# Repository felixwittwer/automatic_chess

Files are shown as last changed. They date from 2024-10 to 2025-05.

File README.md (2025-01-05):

# automatic_chess

## grbl firmware v1.1 for movement

[https://github.com/gnea/grbl](https://github.com/gnea/grbl)

Follow the original guide for installation and compilation: [https://github.com/gnea/grbl/wiki/Compiling-Grbl](https://github.com/gnea/grbl/wiki/Compiling-Grbl)

Instead of the original Repository the cusomt configuration in this repository should be used.

##
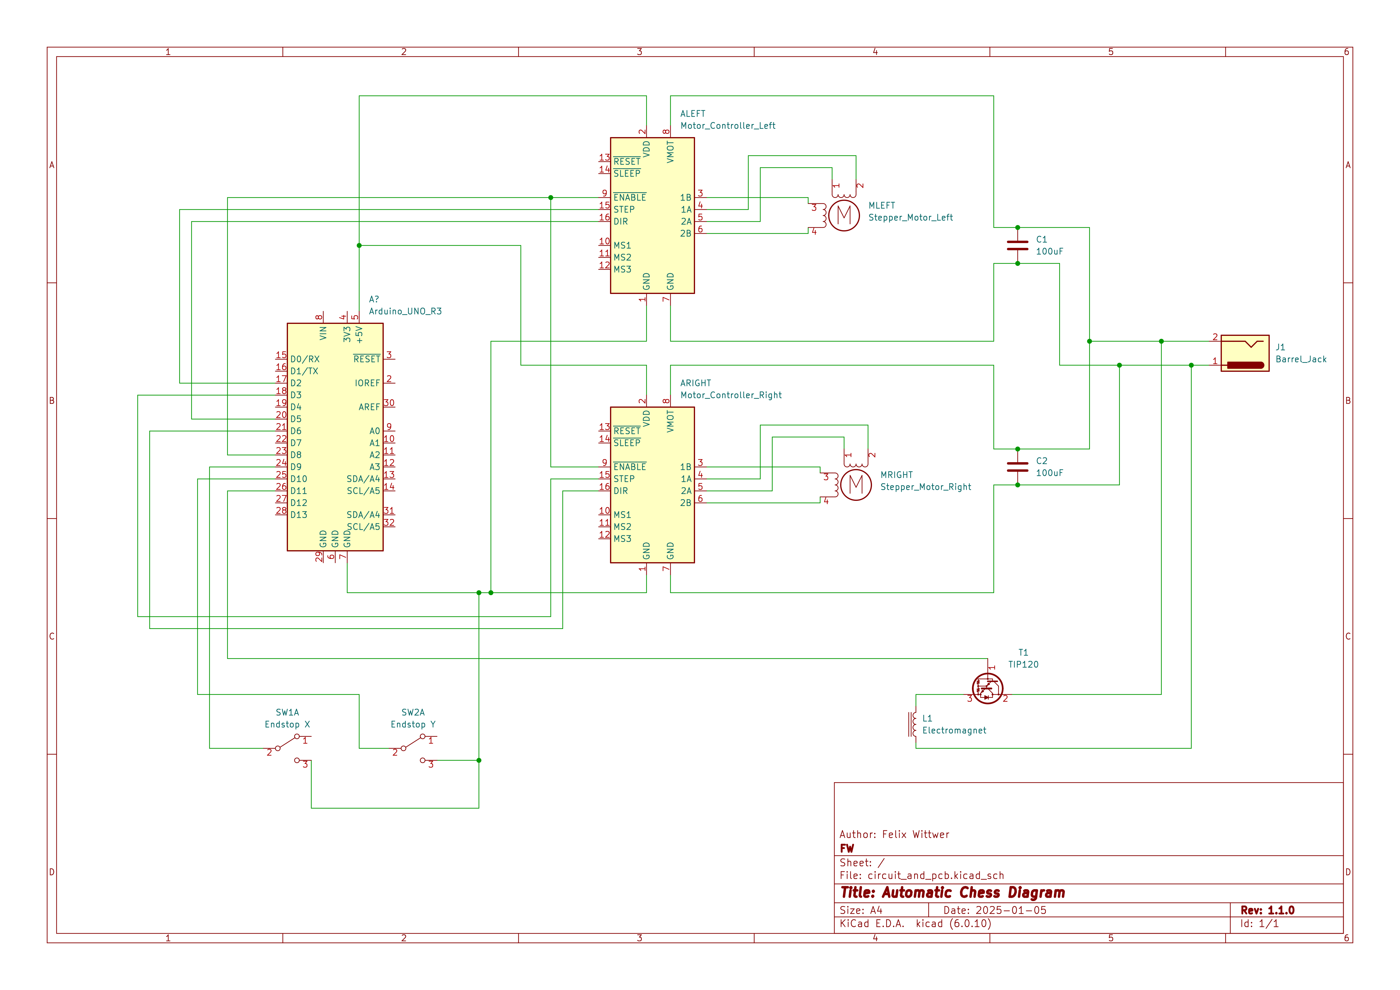
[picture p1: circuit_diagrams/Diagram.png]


[Diagram in PDF form](./circuit_diagrams/Diagram.pdf)

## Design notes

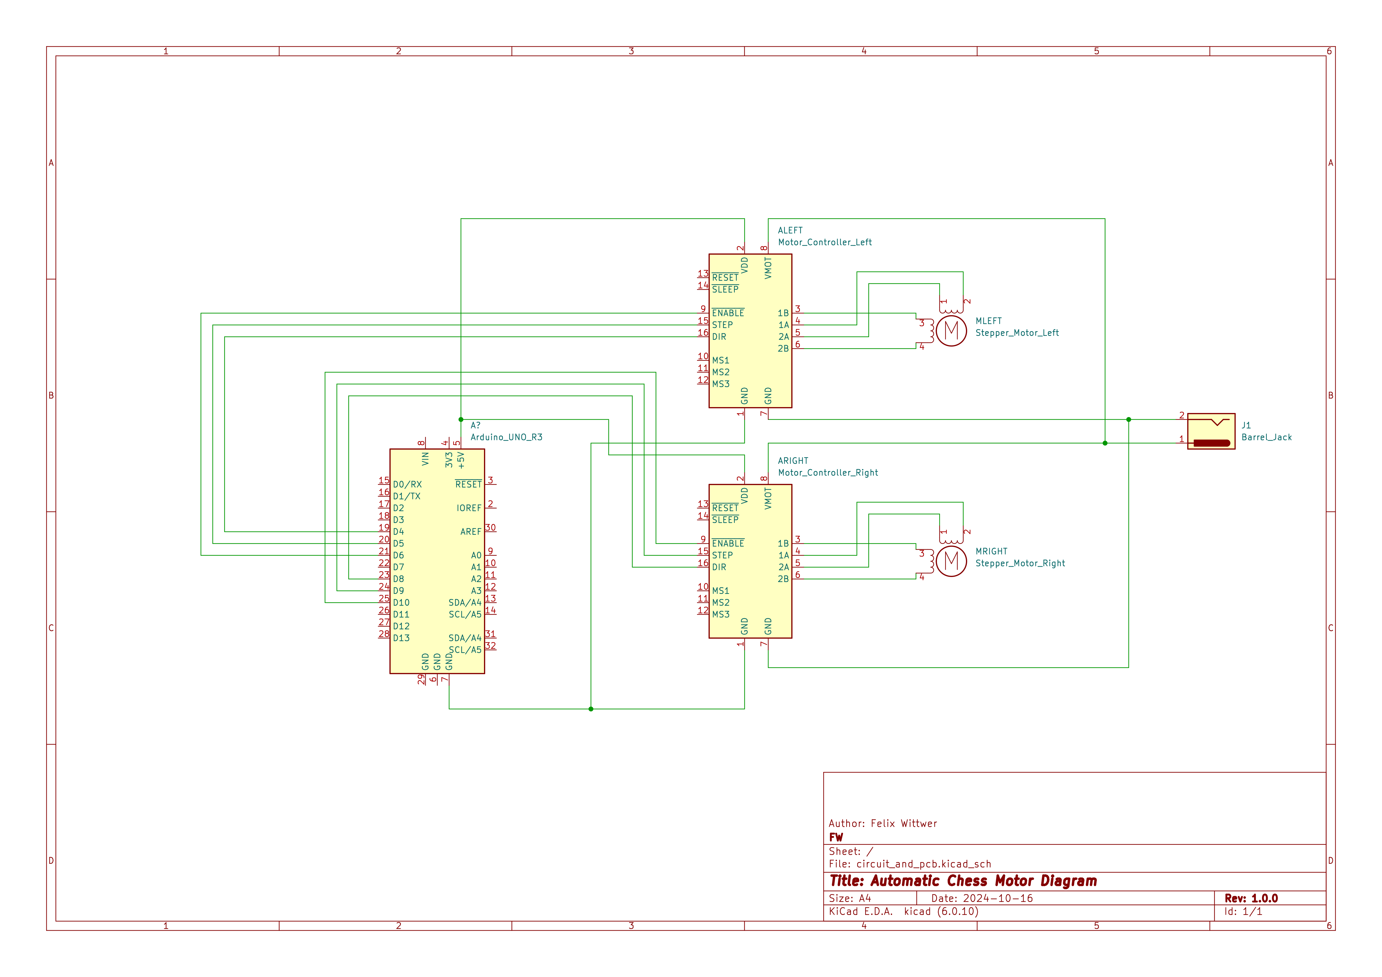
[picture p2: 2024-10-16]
circuit_diagrams/Motor_Diagram.png

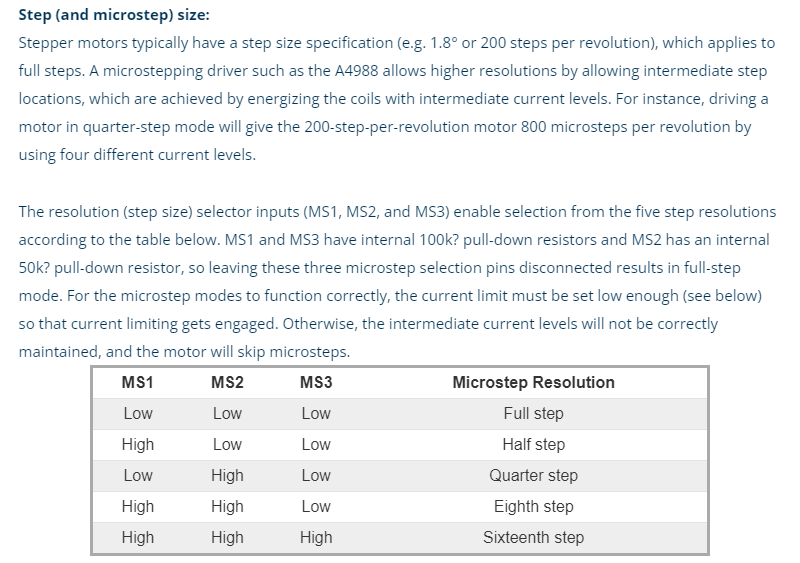
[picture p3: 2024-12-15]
datasheets/motor_driver_A4988/Stepsize.png

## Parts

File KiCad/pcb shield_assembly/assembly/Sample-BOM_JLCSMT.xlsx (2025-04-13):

Comment | Designator | Footprint | JLCPCB Part #（optional）
 | A2.3,A2.1,J17 | PinHeader_1x08_P2.54mm_Vertical
 | A2.4 | PinHeader_1x06_P2.54mm_Vertical
 | A2.2 | PinHeader_1x10_P2.54mm_Vertical
 | A4.2,A4.1,A3.2,A3.1,U4.2,U3.2,U2.2,U1.2 | PinSocket_1x08_P2.54mm_Vertical
 | U4.1,U3.1,U2.1,U1.1 | PinSocket_1x16_P2.54mm_Vertical
 | J14 | TerminalBlock_Phoenix_MKDS-1,5-2_1x02_P5.00mm_Horizontal
 | J4,J2,J6,J3,J8,J5,J1,J7 | PinHeader_2x04_P2.54mm_Vertical
 | J12 | PinHeader_1x02_P2.54mm_Vertical
 | J15,J16 | PinSocket_1x20_P2.54mm_Vertical
 | J19,J18 | PinHeader_1x06_P2.54mm_Vertical
100uF | C1,C2 | CP_Radial_D5.0mm_P2.50mm
 | J13 | PinHeader_1x02_P2.54mm_Vertical
 | J9 | PinHeader_1x02_P2.54mm_Vertical
 | RXD1 | TestPoint_Pad_D2.0mm
TIP120 | Q1 | TO-220-3_Vertical
 | 5V1,5V2 | TestPoint_Pad_D2.0mm
 | GND3,GND2,GND1 | TestPoint_Pad_D2.0mm
 | STEP2,STEP1 | TestPoint_Pad_D2.0mm
 | DIR2,DIR1 | TestPoint_Pad_D2.0mm
 | VMOT1 | TestPoint_Pad_D2.0mm
 | J10 | PinHeader_1x04_P2.54mm_Vertical
 | TXD1 | TestPoint_Pad_D2.0mm
 | J11 | PinHeader_1x04_P2.54mm_Vertical
 | A1 | PinSocket_2x20_P2.54mm_Vertical
100uF | C1 | CAP-SMD_L3.5-W2.8 | C16133

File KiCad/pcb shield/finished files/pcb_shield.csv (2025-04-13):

ID | Bezeichner | Gehäuse | Stückzahl | Bezeichnung | Anbieter und Referenz
1 | J14 | TerminalBlock_Phoenix_MKDS-1,5-2_1x02_P5.00mm_Horizontal | 1 | Barrel_Jack
2 | J4,J2,J6,J3,J8,J5,J1,J7 | PinHeader_2x04_P2.54mm_Vertical | 8
3 | J12 | PinHeader_1x02_P2.54mm_Vertical | 1 | Endstop X
4 | J15,J16 | PinSocket_1x20_P2.54mm_Vertical | 2 | Add Conn
5 | J19,J18 | PinHeader_1x06_P2.54mm_Vertical | 2 | Add Conn
6 | C1,C2 | CP_Radial_D5.0mm_P2.50mm | 2 | 100uF
7 | J13 | PinHeader_1x02_P2.54mm_Vertical | 1 | Endstop Y
8 | J9 | PinHeader_1x02_P2.54mm_Vertical | 1 | E_Magnet
9 | RXD1 | TestPoint_Pad_D2.0mm | 1 | RXD
10 | Q1 | TO-220-3_Vertical | 1 | TIP120
11 | 5V1,5V2 | TestPoint_Pad_D2.0mm | 2 | 5V
12 | GND3,GND2,GND1 | TestPoint_Pad_D2.0mm | 3 | GND
13 | STEP2,STEP1 | TestPoint_Pad_D2.0mm | 2 | STEP
14 | DIR2,DIR1 | TestPoint_Pad_D2.0mm | 2 | DIR
15 | VMOT1 | TestPoint_Pad_D2.0mm | 1 | VMOT
16 | J10 | PinHeader_1x04_P2.54mm_Vertical | 1 | Motor Conn L
17 | TXD1 | TestPoint_Pad_D2.0mm | 1 | TXD
18 | A4 | Pololu_Breakout-16_15.2x20.3mm | 1 | Motor Controller Right
19 | A3 | Pololu_Breakout-16_15.2x20.3mm | 1 | Motor Controller Left
20 | J11 | PinHeader_1x04_P2.54mm_Vertical | 1 | Motor Conn R
21 | J17 | PinHeader_1x08_P2.54mm_Vertical | 1 | Add Conn
22 | U1,U4,U3,U2 | MODULE_BOB-09056 | 4 | BOB-09056
23 | A1 | PinSocket_2x20_P2.54mm_Vertical | 1 | Raspberry Pi Zero
24 | A2 | Arduino_UNO_R3 | 1 | Arduino_UNO_R3

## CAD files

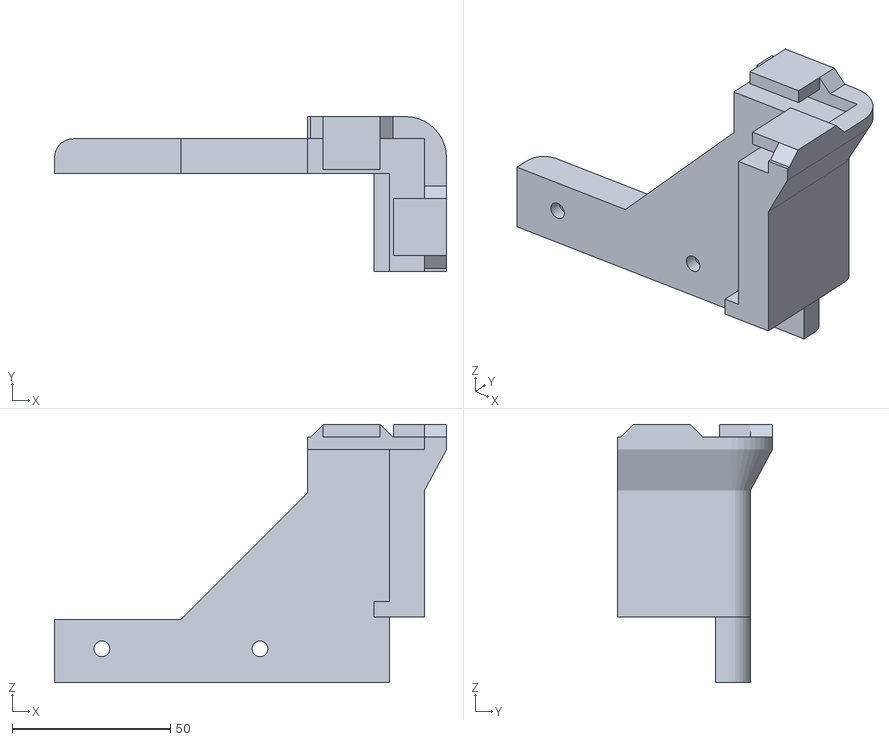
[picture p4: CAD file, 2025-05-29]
3d_files/Plexiglasmount/A_Plexiglasmount.stl
124.0 x 49.0 x 81.7

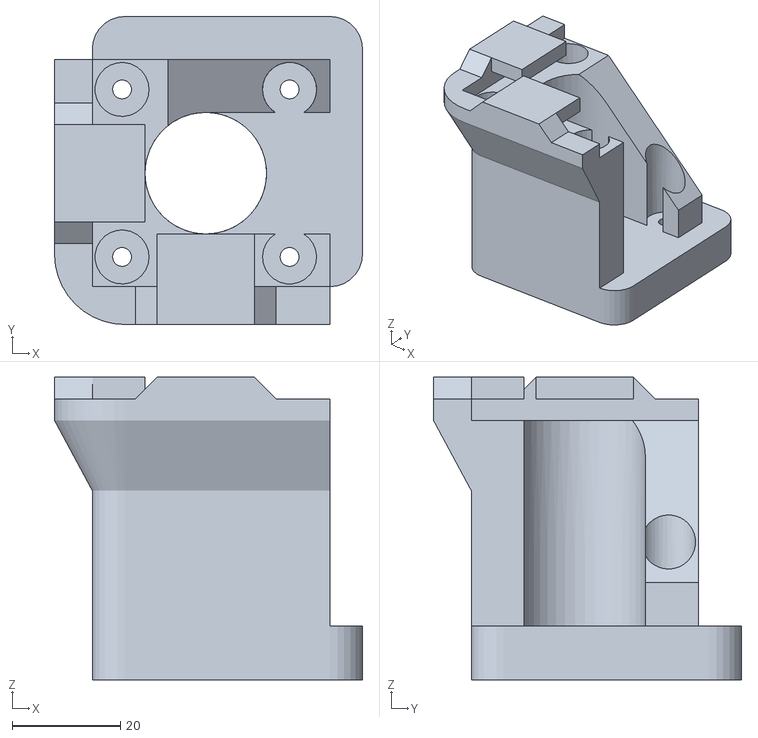
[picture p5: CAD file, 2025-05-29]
3d_files/Plexiglasmount/Motor_B_Plexiglasmount.stl
57.0 x 57.0 x 56.0

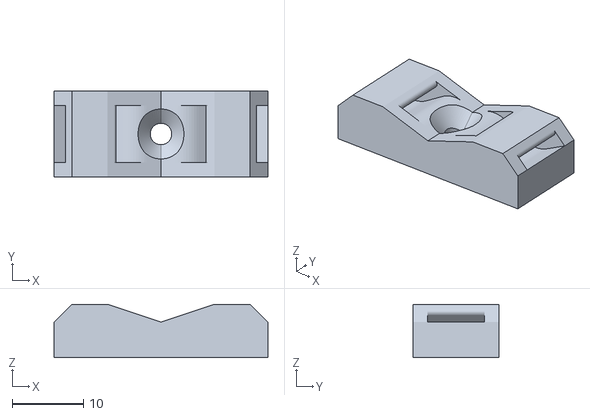
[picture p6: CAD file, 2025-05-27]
3d_files/PCB holder and cable organizers/Cable_clips_for_zipties.stl
30.0 x 12.0 x 7.50

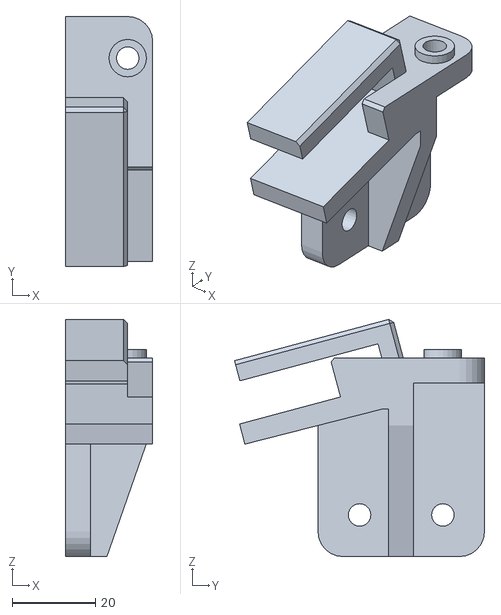
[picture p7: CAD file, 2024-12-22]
3d_files/Pulley_Support_A_new.stl
21.0 x 60.1 x 57.0

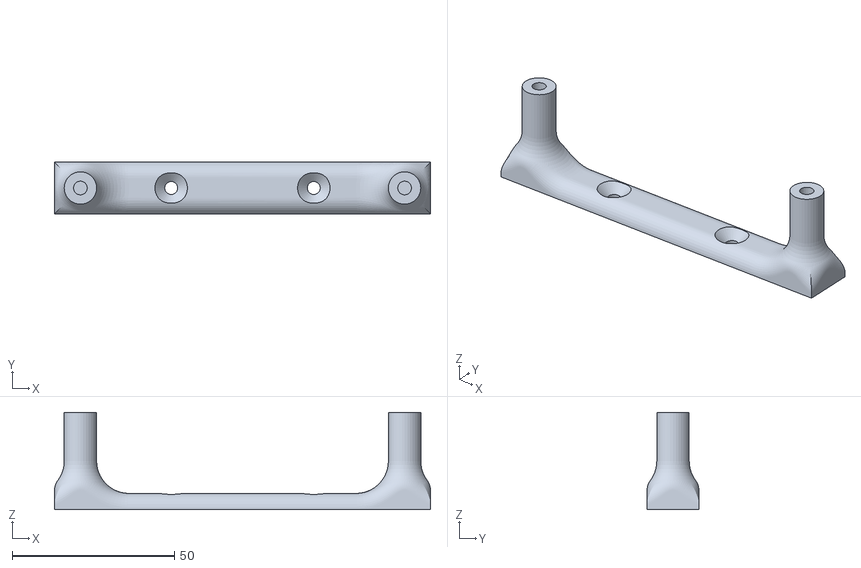
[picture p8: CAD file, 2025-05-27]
3d_files/PCB holder and cable organizers/PCB_holder.stl
116.0 x 16.0 x 30.0

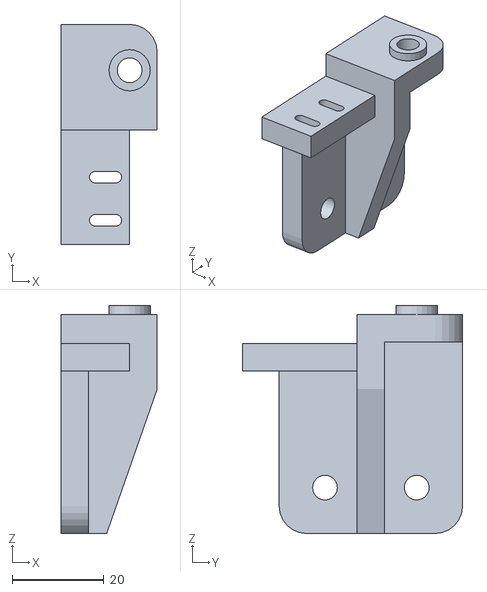
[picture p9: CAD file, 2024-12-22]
3d_files/Pulley_Support_A.stl
21.0 x 48.0 x 49.7

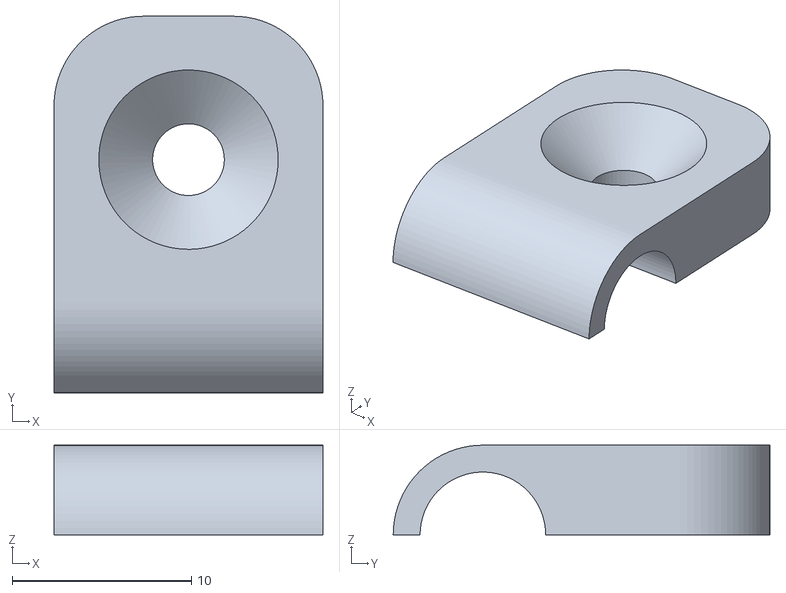
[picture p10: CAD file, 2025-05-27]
3d_files/PCB holder and cable organizers/small cable clip.stl
15.0 x 21.0 x 5.00

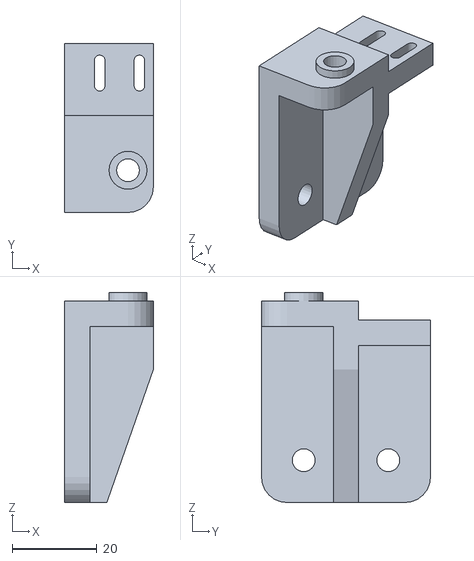
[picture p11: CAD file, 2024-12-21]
3d_files/Pulley_Support_B.stl
21.0 x 40.0 x 49.7

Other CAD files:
3d_files/Plexiglasmount/Motor_A_Plexiglasmount.stl
3d_files/Plexiglasmount/B_Plexiglasmount.stl
3d_files/Pulley_Support_B_new.stl

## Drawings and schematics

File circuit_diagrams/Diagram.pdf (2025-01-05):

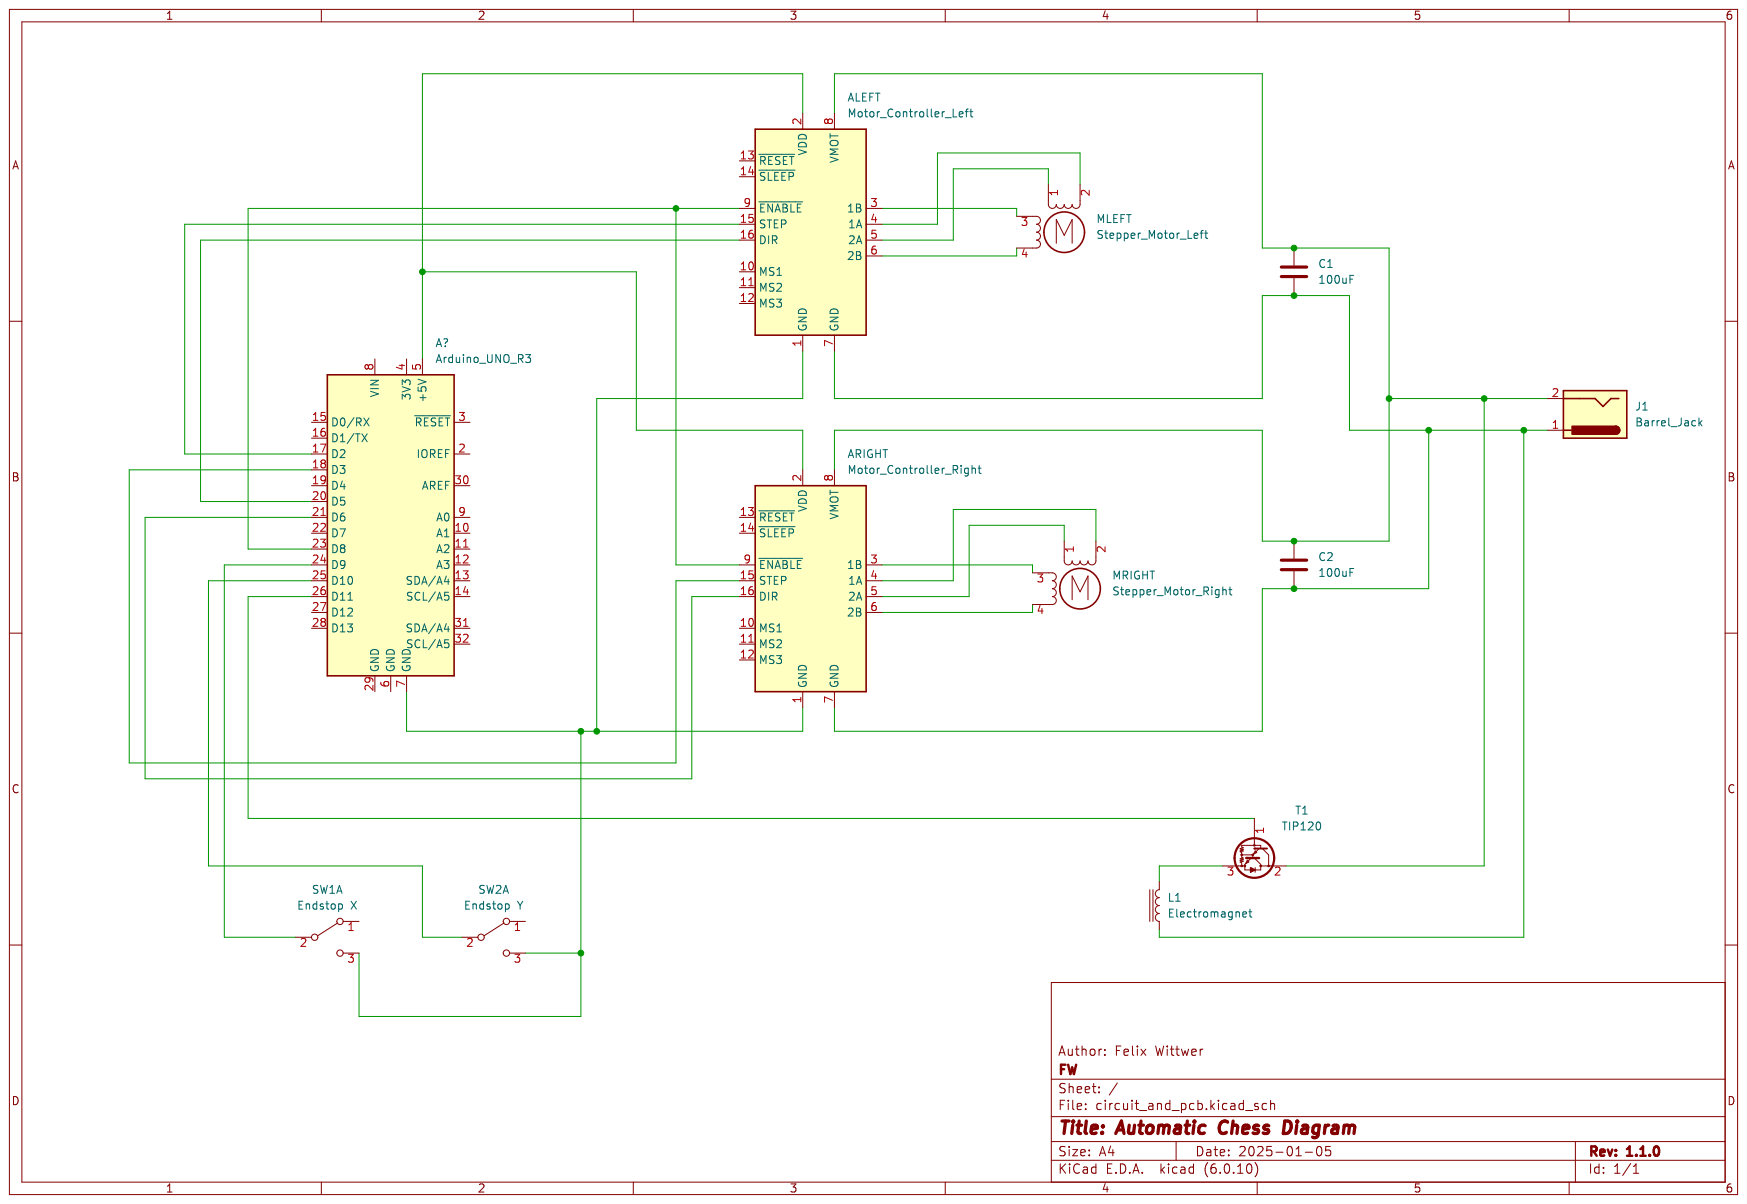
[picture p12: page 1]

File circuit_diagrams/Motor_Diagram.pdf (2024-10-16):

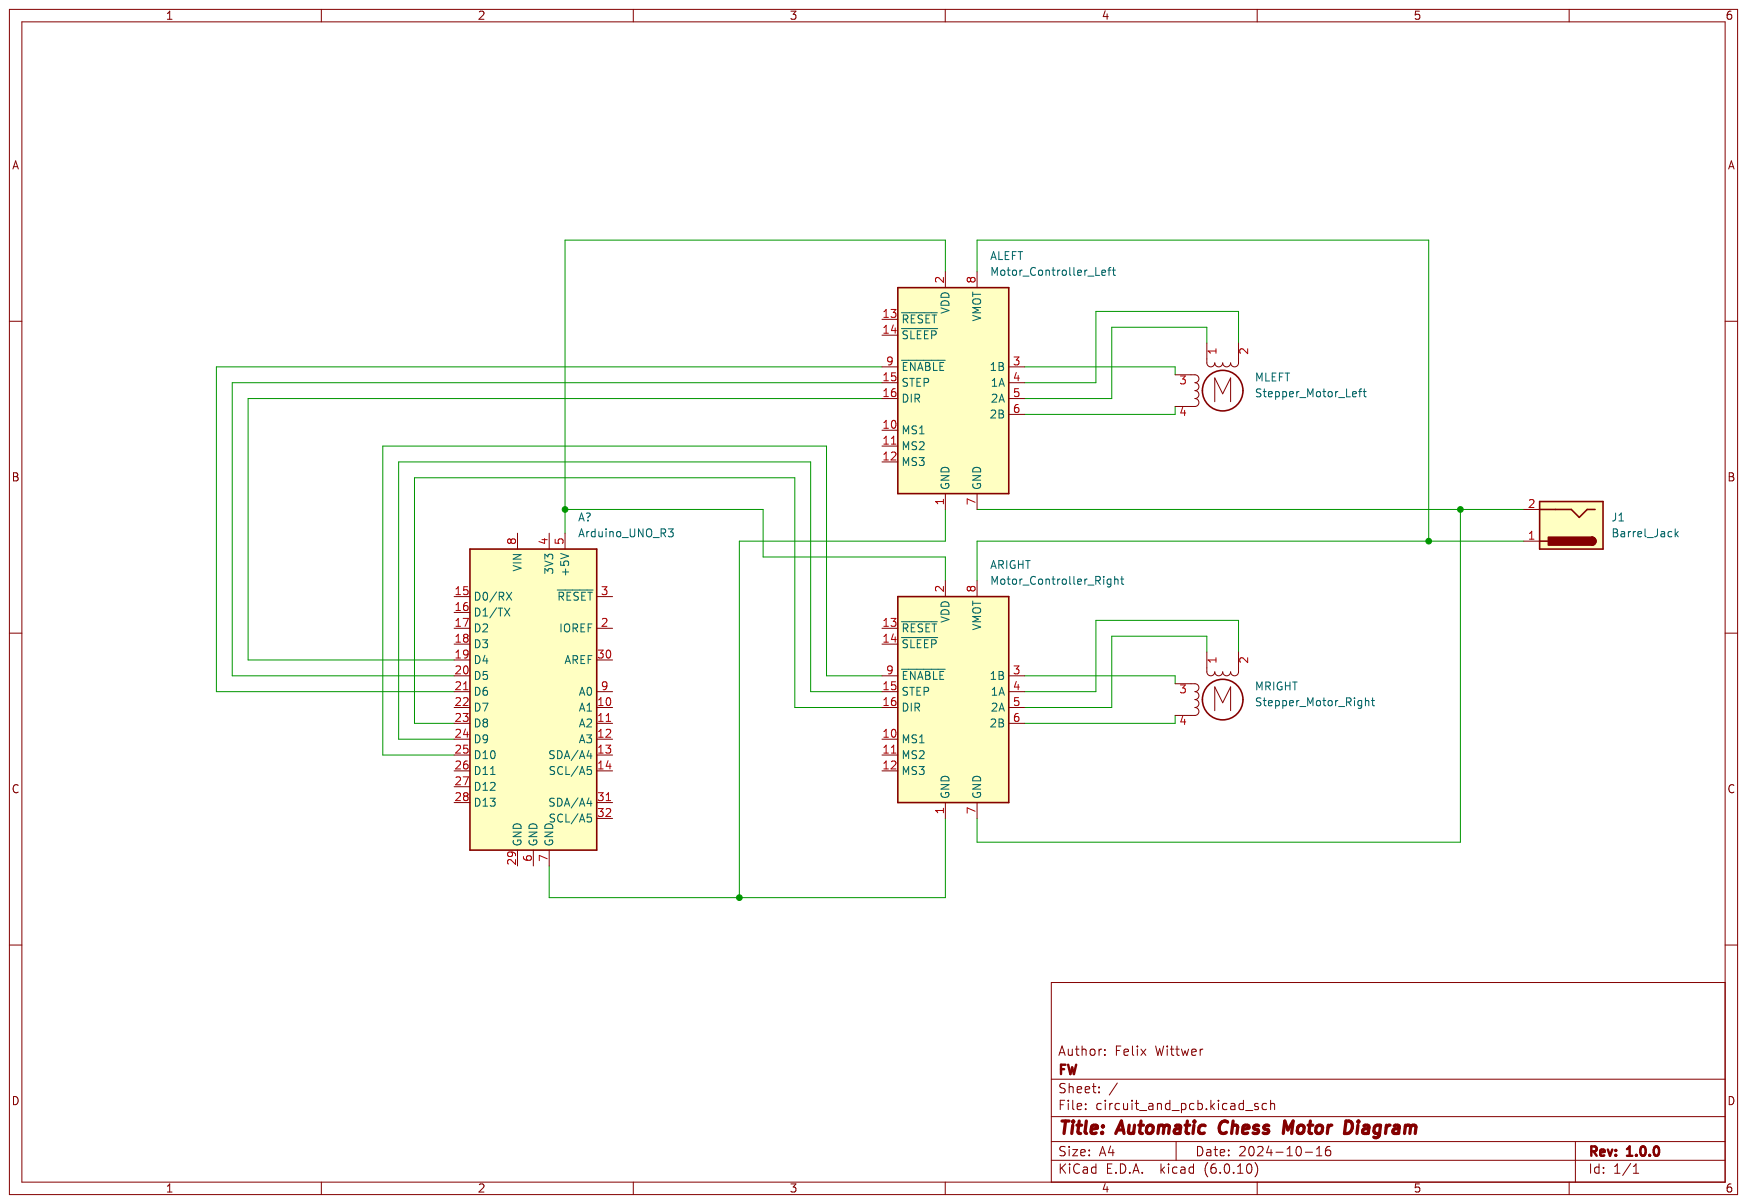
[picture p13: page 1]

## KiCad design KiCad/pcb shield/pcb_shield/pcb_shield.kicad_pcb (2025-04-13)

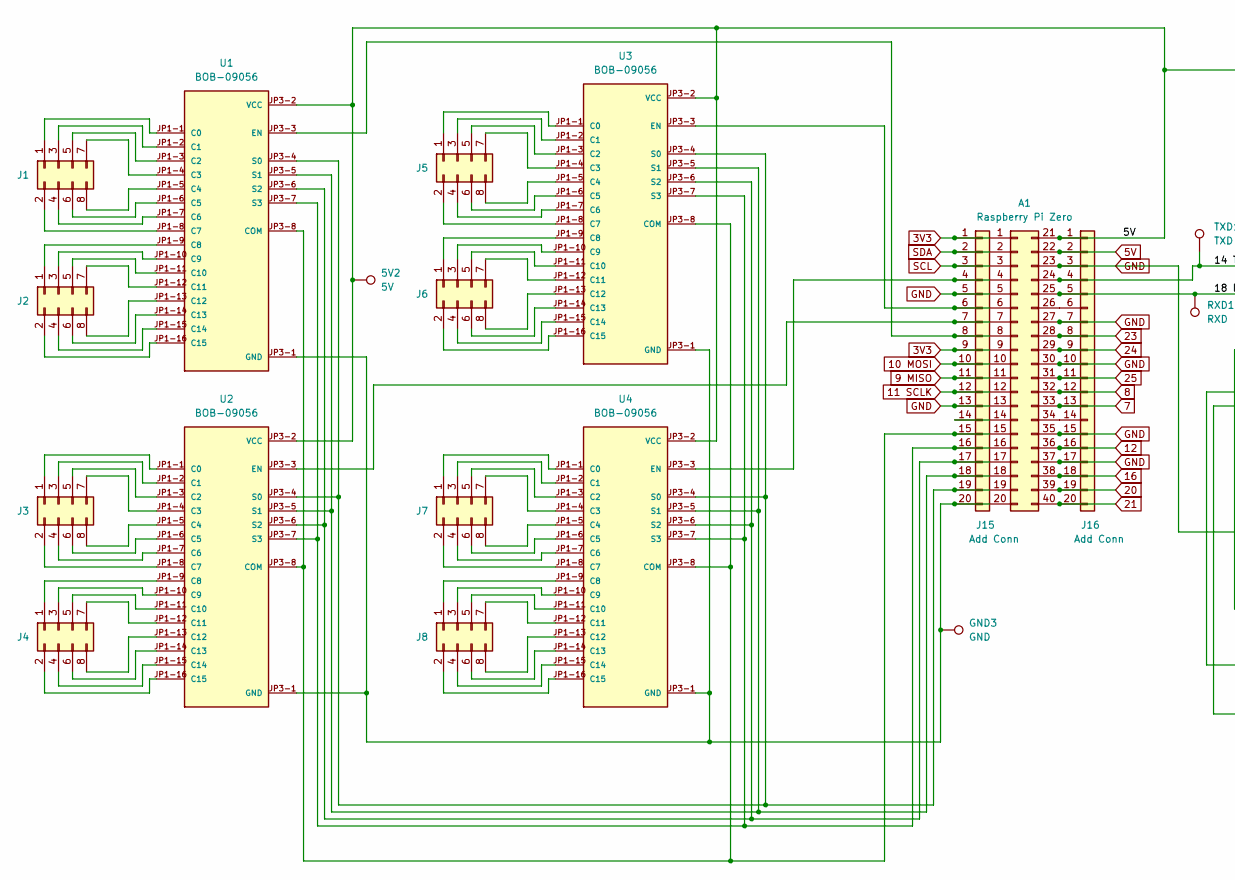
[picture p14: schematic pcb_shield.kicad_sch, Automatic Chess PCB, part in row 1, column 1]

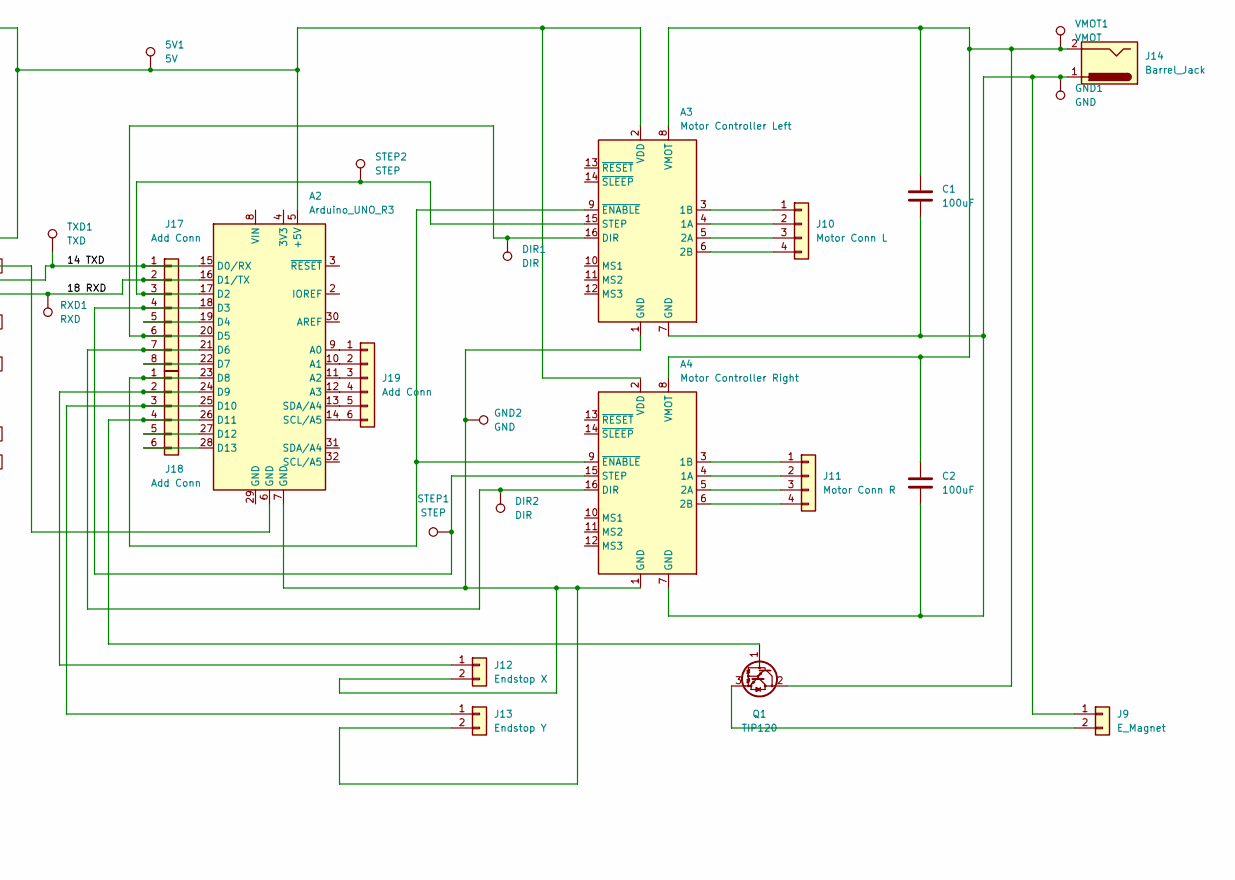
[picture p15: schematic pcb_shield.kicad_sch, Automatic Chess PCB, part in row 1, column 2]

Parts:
5V1, 5V2: 5V; TestPoint_Pad_D2.0mm
A1: Raspberry Pi Zero; PinSocket_2x20_P2.54mm_Vertical
A2: Arduino_UNO_R3
A3: Motor Controller Left; Pololu_Breakout-16_15.2x20.3mm
A4: Motor Controller Right; Pololu_Breakout-16_15.2x20.3mm
C1, C2: 100uF; CP_Radial_D5.0mm_P2.50mm
DIR1, DIR2: DIR; TestPoint_Pad_D2.0mm
GND1, GND2, GND3: GND; TestPoint_Pad_D2.0mm
J1, J2, J3, J4, J5, J6, J7, J8: PinHeader_2x04_P2.54mm_Vertical
J9: E_Magnet; PinHeader_1x02_P2.54mm_Vertical
J10: Motor Conn L; PinHeader_1x04_P2.54mm_Vertical
J11: Motor Conn R; PinHeader_1x04_P2.54mm_Vertical
J12: Endstop X; PinHeader_1x02_P2.54mm_Vertical
J13: Endstop Y; PinHeader_1x02_P2.54mm_Vertical
J14: Barrel_Jack; TerminalBlock_Phoenix_MKDS-1,5-2_1x02_P5.00mm_Horizontal
J15, J16: Add Conn; PinSocket_1x20_P2.54mm_Vertical
J17: Add Conn; PinHeader_1x08_P2.54mm_Vertical
J18, J19: Add Conn; PinHeader_1x06_P2.54mm_Vertical
Q1: TIP120; TO-220-3_Vertical
RXD1: RXD; TestPoint_Pad_D2.0mm
STEP1, STEP2: STEP; TestPoint_Pad_D2.0mm
TXD1: TXD; TestPoint_Pad_D2.0mm
U1, U2, U3, U4: BOB-09056; MODULE_BOB-09056; PARTREV v11
VMOT1: VMOT; TestPoint_Pad_D2.0mm

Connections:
3V3: A1.1, A1.9, J15.1, J15.9
5V: 5V1.1, 5V2.1, A1.21, A1.22, A2.5 (+5V), A3.2 (VDD), A4.2 (VDD), J16.1, J16.2, U1.JP3-2 (VCC), U2.JP3-2 (VCC), U3.JP3-2 (VCC), U4.JP3-2 (VCC)
7: A1.33, J16.13
8: A1.32, J16.12
9 MISO: A1.11, J15.11
10 MOSI: A1.10, J15.10
11 SCLK: A1.12, J15.12
12: A1.36, J16.16
16: A1.38, J16.18
20: A1.39, J16.19
21: A1.40, J16.20
23: A1.28, J16.8
24: A1.29, J16.9
25: A1.31, J16.11
/14 TXD: A1.24, A2.15 (D0/RX), J16.4, J17.1, TXD1.1
/18 RXD: A1.25, A2.16 (D1/TX), J16.5, J17.2, RXD1.1
GND: A1.5, A1.13, A1.23, A1.27, A1.30, A1.35, A1.37, A2.6 (GND), J15.5, J15.13, J16.3, J16.7, J16.10, J16.15, J16.17
unnamed: A1.4, J15.4, U4.JP3-3 (EN)
unnamed: A1.6, J15.6, U3.JP3-3 (EN)
unnamed: A1.7, J15.7, U2.JP3-3 (EN)
unnamed: A1.8, J15.8, U1.JP3-3 (EN)
unnamed: A1.14, J15.14
unnamed: A1.15, J15.15, U1.JP3-8 (COM), U2.JP3-8 (COM), U3.JP3-8 (COM), U4.JP3-8 (COM)
unnamed: A1.16, J15.16, U1.JP3-7 (S3), U2.JP3-7 (S3), U3.JP3-7 (S3), U4.JP3-7 (S3)
unnamed: A1.17, J15.17, U1.JP3-6 (S2), U2.JP3-6 (S2), U3.JP3-6 (S2), U4.JP3-6 (S2)
unnamed: A1.18, J15.18, U1.JP3-5 (S1), U2.JP3-5 (S1), U3.JP3-5 (S1), U4.JP3-5 (S1)
unnamed: A1.19, J15.19, U1.JP3-4 (S0), U2.JP3-4 (S0), U3.JP3-4 (S0), U4.JP3-4 (S0)
unnamed: A1.20, GND3.1, J15.20, U1.JP3-1 (GND), U2.JP3-1 (GND), U3.JP3-1 (GND), U4.JP3-1 (GND)
unnamed: A1.26, J16.6
unnamed: A1.34, J16.14
unnamed: A2.7 (GND), A3.1 (GND), A4.1 (GND), GND2.1, J12.2, J13.2
unnamed: A2.9 (A0), J19.1
unnamed: A2.10 (A1), J19.2
unnamed: A2.11 (A2), J19.3
unnamed: A2.12 (A3), J19.4
unnamed: A2.13 (SDA/A4), J19.5
unnamed: A2.14 (SCL/A5), J19.6
unnamed: A2.17 (D2), A3.15 (STEP), J17.3, STEP2.1
unnamed: A2.18 (D3), A4.15 (STEP), J17.4, STEP1.1
unnamed: A2.19 (D4), J17.5
unnamed: A2.20 (D5), A3.16 (DIR), DIR1.1, J17.6
unnamed: A2.21 (D6), A4.16 (DIR), DIR2.1, J17.7
unnamed: A2.22 (D7), J17.8
unnamed: A2.23 (D8), A3.9 (~ENABLE), A4.9 (~ENABLE), J18.1
unnamed: A2.24 (D9), J12.1, J18.2
unnamed: A2.25 (D10), J13.1, J18.3
unnamed: A2.26 (D11), J18.4, Q1.1 (B)
unnamed: A2.27 (D12), J18.5
unnamed: A2.28 (D13), J18.6
unnamed: A3.3 (1B), J10.1
unnamed: A3.4 (1A), J10.2
unnamed: A3.5 (2A), J10.3
unnamed: A3.6 (2B), J10.4
unnamed: A3.7 (GND), A4.7 (GND), C1.2, C2.2, GND1.1, J9.1, J14.1
unnamed: A3.8 (VMOT), A4.8 (VMOT), C1.1, C2.1, J14.2, Q1.2 (C), VMOT1.1
unnamed: A4.3 (1B), J11.1
unnamed: A4.4 (1A), J11.2
unnamed: A4.5 (2A), J11.3
unnamed: A4.6 (2B), J11.4
unnamed: J1.1, U1.JP1-1 (C0)
unnamed: J1.2, U1.JP1-8 (C7)
unnamed: J1.3, U1.JP1-2 (C1)
unnamed: J1.4, U1.JP1-7 (C6)
unnamed: J1.5, U1.JP1-3 (C2)
unnamed: J1.6, U1.JP1-6 (C5)
unnamed: J1.7, U1.JP1-4 (C3)
unnamed: J1.8, U1.JP1-5 (C4)
unnamed: J2.1, U1.JP1-9 (C8)
unnamed: J2.2, U1.JP1-16 (C15)
unnamed: J2.3, U1.JP1-10 (C9)
unnamed: J2.4, U1.JP1-15 (C14)
unnamed: J2.5, U1.JP1-11 (C10)
unnamed: J2.6, U1.JP1-14 (C13)
unnamed: J2.7, U1.JP1-12 (C11)
unnamed: J2.8, U1.JP1-13 (C12)
unnamed: J3.1, U2.JP1-1 (C0)
unnamed: J3.2, U2.JP1-8 (C7)
unnamed: J3.3, U2.JP1-2 (C1)
unnamed: J3.4, U2.JP1-7 (C6)
unnamed: J3.5, U2.JP1-3 (C2)
unnamed: J3.6, U2.JP1-6 (C5)
unnamed: J3.7, U2.JP1-4 (C3)
unnamed: J3.8, U2.JP1-5 (C4)
unnamed: J4.1, U2.JP1-9 (C8)
unnamed: J4.2, U2.JP1-16 (C15)
unnamed: J4.3, U2.JP1-10 (C9)
unnamed: J4.4, U2.JP1-15 (C14)
unnamed: J4.5, U2.JP1-11 (C10)
unnamed: J4.6, U2.JP1-14 (C13)
unnamed: J4.7, U2.JP1-12 (C11)
unnamed: J4.8, U2.JP1-13 (C12)
unnamed: J5.1, U3.JP1-1 (C0)
unnamed: J5.2, U3.JP1-8 (C7)
unnamed: J5.3, U3.JP1-2 (C1)
unnamed: J5.4, U3.JP1-7 (C6)
unnamed: J5.5, U3.JP1-3 (C2)
unnamed: J5.6, U3.JP1-6 (C5)
unnamed: J5.7, U3.JP1-4 (C3)
unnamed: J5.8, U3.JP1-5 (C4)
unnamed: J6.1, U3.JP1-9 (C8)
unnamed: J6.2, U3.JP1-16 (C15)
unnamed: J6.3, U3.JP1-10 (C9)
unnamed: J6.4, U3.JP1-15 (C14)
unnamed: J6.5, U3.JP1-11 (C10)
unnamed: J6.6, U3.JP1-14 (C13)
unnamed: J6.7, U3.JP1-12 (C11)
unnamed: J6.8, U3.JP1-13 (C12)
unnamed: J7.1, U4.JP1-1 (C0)
unnamed: J7.2, U4.JP1-8 (C7)
unnamed: J7.3, U4.JP1-2 (C1)
unnamed: J7.4, U4.JP1-7 (C6)
unnamed: J7.5, U4.JP1-3 (C2)
unnamed: J7.6, U4.JP1-6 (C5)
unnamed: J7.7, U4.JP1-4 (C3)
unnamed: J7.8, U4.JP1-5 (C4)
unnamed: J8.1, U4.JP1-9 (C8)
unnamed: J8.2, U4.JP1-16 (C15)
unnamed: J8.3, U4.JP1-10 (C9)
unnamed: J8.4, U4.JP1-15 (C14)
unnamed: J8.5, U4.JP1-11 (C10)
unnamed: J8.6, U4.JP1-14 (C13)
unnamed: J8.7, U4.JP1-12 (C11)
unnamed: J8.8, U4.JP1-13 (C12)
unnamed: J9.2, Q1.3 (E)
SCL: A1.3, J15.3
SDA: A1.2, J15.2

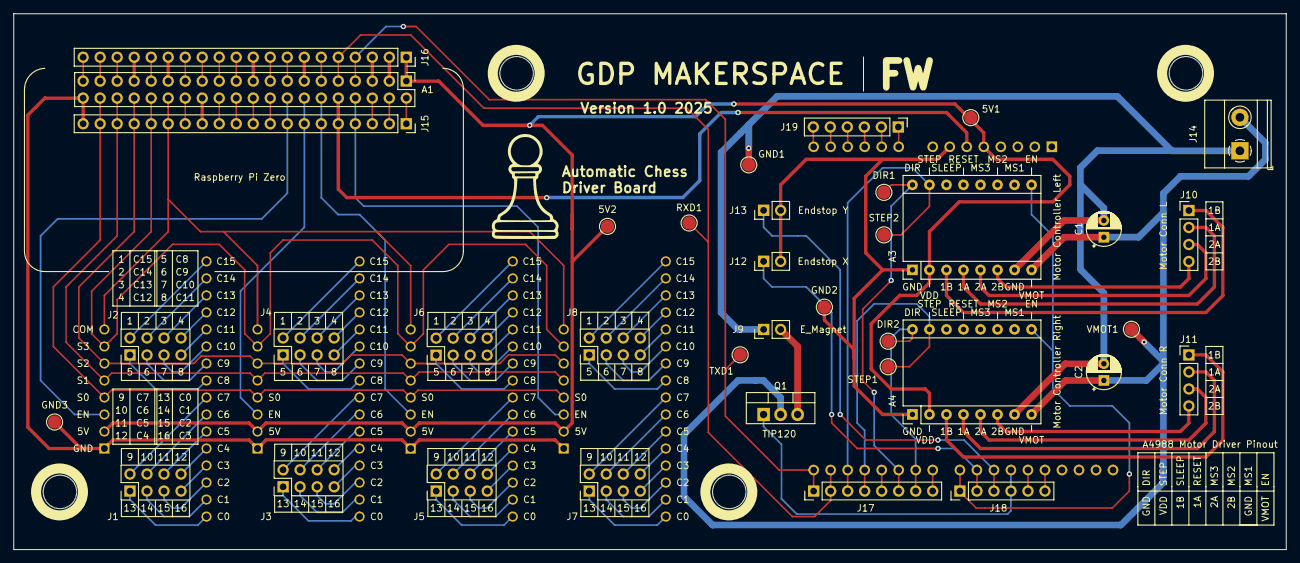
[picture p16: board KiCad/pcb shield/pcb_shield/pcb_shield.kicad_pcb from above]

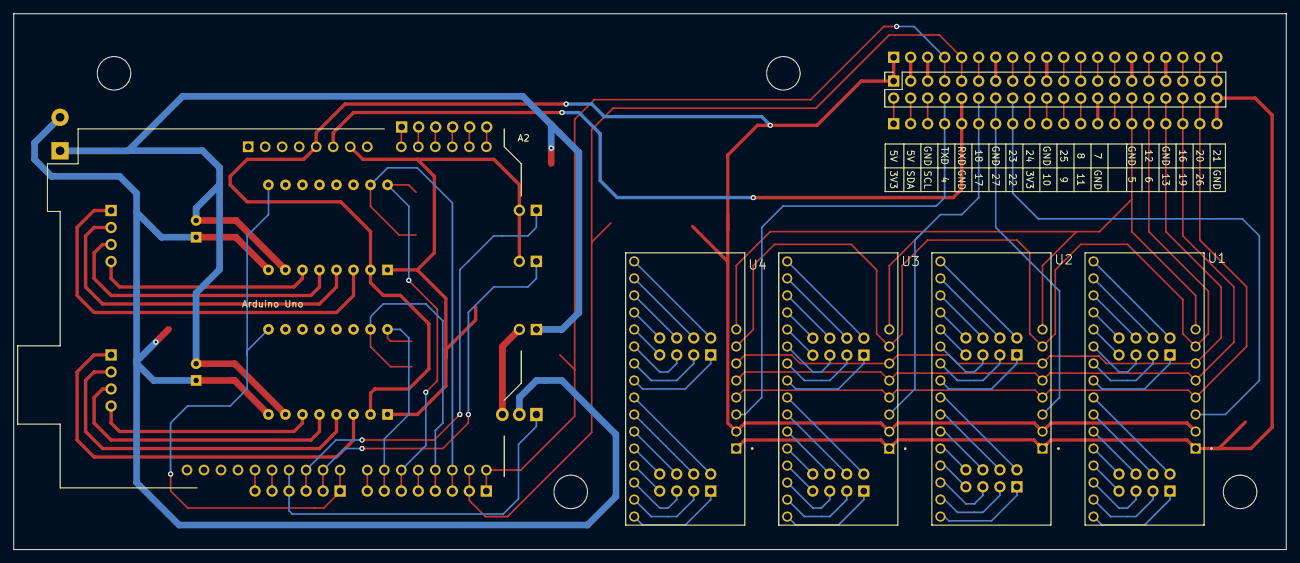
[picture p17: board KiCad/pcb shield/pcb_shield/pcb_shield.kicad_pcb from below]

Board: 2 copper layers, 190.0 x 80.0 mm, 42 parts (6 on the bottom side), 126 nets.

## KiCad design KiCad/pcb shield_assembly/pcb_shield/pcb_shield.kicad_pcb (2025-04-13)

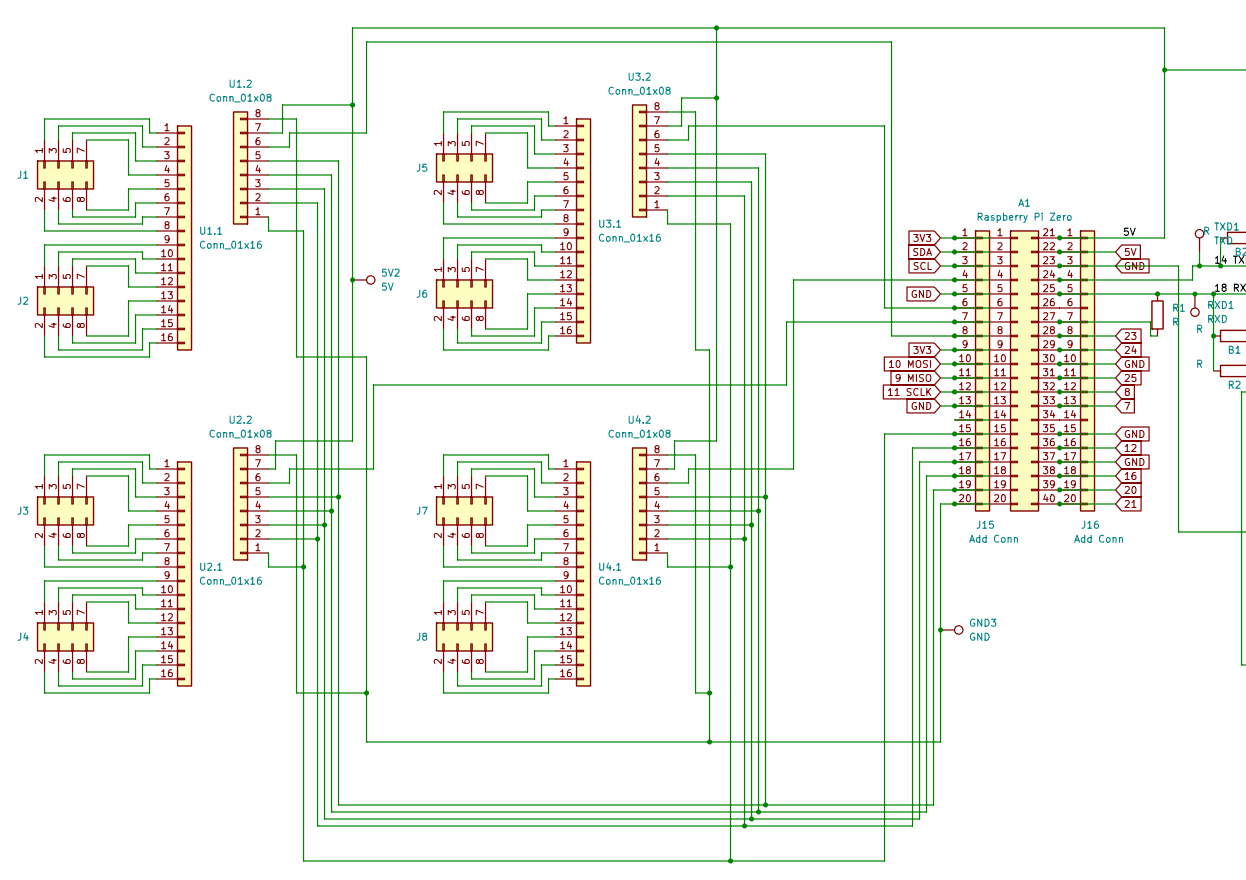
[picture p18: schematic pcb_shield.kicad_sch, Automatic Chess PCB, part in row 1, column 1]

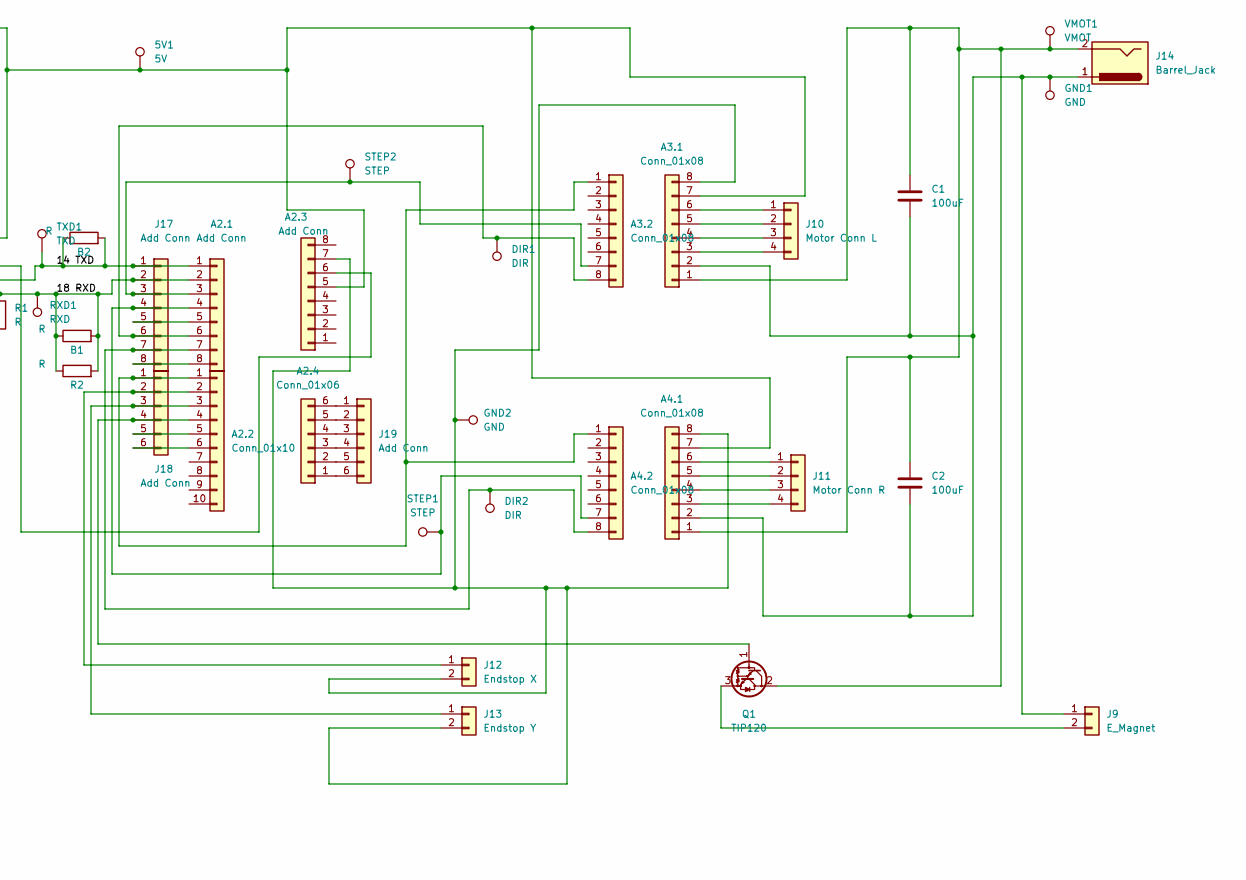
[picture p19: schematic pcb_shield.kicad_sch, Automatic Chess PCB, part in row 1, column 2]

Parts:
5V1, 5V2: 5V; TestPoint_Pad_D2.0mm
A1: Raspberry Pi Zero; PinSocket_2x20_P2.54mm_Vertical
A2.1, A2.3: Add Conn; PinHeader_1x08_P2.54mm_Vertical
A2.2: Conn_01x10; PinHeader_1x10_P2.54mm_Vertical
A2.4: Conn_01x06; PinHeader_1x06_P2.54mm_Vertical
A3.1, A3.2, A4.1, A4.2: Conn_01x08; PinSocket_1x08_P2.54mm_Vertical
B1, B2: R; R_1206_3216Metric_Pad1.30x1.75mm_HandSolder
C1, C2: 100uF; CP_Radial_D5.0mm_P2.50mm
DIR1, DIR2: DIR; TestPoint_Pad_D2.0mm
GND1, GND2, GND3: GND; TestPoint_Pad_D2.0mm
J1, J2, J3, J4, J5, J6, J7, J8: PinHeader_2x04_P2.54mm_Vertical
J9: E_Magnet; PinHeader_1x02_P2.54mm_Vertical
J10: Motor Conn L; PinHeader_1x04_P2.54mm_Vertical
J11: Motor Conn R; PinHeader_1x04_P2.54mm_Vertical
J12: Endstop X; PinHeader_1x02_P2.54mm_Vertical
J13: Endstop Y; PinHeader_1x02_P2.54mm_Vertical
J14: Barrel_Jack; TerminalBlock_Phoenix_MKDS-1,5-2_1x02_P5.00mm_Horizontal
J15, J16: Add Conn; PinSocket_1x20_P2.54mm_Vertical
J17: Add Conn; PinHeader_1x08_P2.54mm_Vertical
J18, J19: Add Conn; PinHeader_1x06_P2.54mm_Vertical
Q1: TIP120; TO-220-3_Vertical
R1, R2: R; R_Axial_DIN0309_L9.0mm_D3.2mm_P12.70mm_Horizontal
RXD1: RXD; TestPoint_Pad_D2.0mm
STEP1, STEP2: STEP; TestPoint_Pad_D2.0mm
TXD1: TXD; TestPoint_Pad_D2.0mm
U1.1, U2.1, U3.1, U4.1: Conn_01x16; PinSocket_1x16_P2.54mm_Vertical
U1.2, U2.2, U3.2, U4.2: Conn_01x08; PinSocket_1x08_P2.54mm_Vertical
VMOT1: VMOT; TestPoint_Pad_D2.0mm

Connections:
3V3: A1.1, A1.9, J15.1, J15.9
5V: 5V1.1, 5V2.1, A1.21, A1.22, A2.3.5, A3.1.7, A4.1.7, J16.1, J16.2, U1.2.7, U2.2.7, U3.2.7, U4.2.7
7: A1.33, J16.13
8: A1.32, J16.12
9 MISO: A1.11, J15.11
10 MOSI: A1.10, J15.10
11 SCLK: A1.12, J15.12
12: A1.36, J16.16
16: A1.38, J16.18
20: A1.39, J16.19
21: A1.40, J16.20
23: A1.28, J16.8
24: A1.29, J16.9
25: A1.31, J16.11
/14 TXD: A1.24, A2.1.1, B2.1, B2.2, J16.4, J17.1, TXD1.1
/18 RXD: A1.25, A2.1.2, B1.1, B1.2, J16.5, J17.2, R1.1, R2.1, R2.2, RXD1.1
GND: A1.5, A1.13, A1.23, A1.30, A1.35, A1.37, A2.3.6, J15.5, J15.13, J16.3, J16.10, J16.15, J16.17
unnamed: A1.4, J15.4, U4.2.6
unnamed: A1.6, J15.6, U3.2.6
unnamed: A1.7, J15.7, U2.2.6
unnamed: A1.14, J15.14
unnamed: A1.15, J15.15, U1.2.1, U2.2.1, U3.2.1, U4.2.1
unnamed: A1.16, J15.16, U1.2.2, U2.2.2, U3.2.2, U4.2.2
unnamed: A1.17, J15.17, U1.2.3, U2.2.3, U3.2.3, U4.2.3
unnamed: A1.18, J15.18, U1.2.4, U2.2.4, U3.2.4, U4.2.4
unnamed: A1.19, J15.19, U1.2.5, U2.2.5, U3.2.5, U4.2.5
unnamed: A1.20, GND3.1, J15.20, U1.2.8, U2.2.8, U3.2.8, U4.2.8
unnamed: A1.26, J16.6
unnamed: A1.27, J16.7, R1.2
unnamed: A1.34, J16.14
unnamed: A2.3.7, A3.1.8, A4.1.8, GND2.1, J12.2, J13.2
unnamed: A3.1.1, A4.1.1, C1.1, C2.1, J14.2, Q1.2 (C), VMOT1.1
unnamed: A3.1.2, A4.1.2, C1.2, C2.2, GND1.1, J9.1, J14.1
unnamed: A3.1.3, J10.4
unnamed: A3.1.4, J10.3
unnamed: A3.1.5, J10.2
unnamed: A3.1.6, J10.1
unnamed: A2.2.1, A3.2.1, A4.2.1, J18.1
unnamed: A2.1.3, A3.2.7, J17.3, STEP2.1
unnamed: A2.1.6, A3.2.8, DIR1.1, J17.6
unnamed: A2.1.4, A4.2.7, J17.4, STEP1.1
unnamed: A2.1.7, A4.2.8, DIR2.1, J17.7
unnamed: J1.1, U1.1.1
unnamed: J1.2, U1.1.8
unnamed: J1.3, U1.1.2
unnamed: J1.4, U1.1.7
unnamed: J1.5, U1.1.3
unnamed: J1.6, U1.1.6
unnamed: J1.7, U1.1.4
unnamed: J1.8, U1.1.5
unnamed: J2.1, U1.1.9
unnamed: J2.2, U1.1.16
unnamed: J2.3, U1.1.10
unnamed: J2.4, U1.1.15
unnamed: J2.5, U1.1.11
unnamed: J2.6, U1.1.14
unnamed: J2.7, U1.1.12
unnamed: J2.8, U1.1.13
unnamed: J3.1, U2.1.1
unnamed: J3.2, U2.1.8
unnamed: J3.3, U2.1.2
unnamed: J3.4, U2.1.7
unnamed: J3.5, U2.1.3
unnamed: J3.6, U2.1.6
unnamed: J3.7, U2.1.4
unnamed: J3.8, U2.1.5
unnamed: J4.1, U2.1.9
unnamed: J4.2, U2.1.16
unnamed: J4.3, U2.1.10
unnamed: J4.4, U2.1.15
unnamed: J4.5, U2.1.11
unnamed: J4.6, U2.1.14
unnamed: J4.7, U2.1.12
unnamed: J4.8, U2.1.13
unnamed: J5.1, U3.1.1
unnamed: J5.2, U3.1.8
unnamed: J5.3, U3.1.2
unnamed: J5.4, U3.1.7
unnamed: J5.5, U3.1.3
unnamed: J5.6, U3.1.6
unnamed: J5.7, U3.1.4
unnamed: J5.8, U3.1.5
unnamed: J6.1, U3.1.9
unnamed: J6.2, U3.1.16
unnamed: J6.3, U3.1.10
unnamed: J6.4, U3.1.15
unnamed: J6.5, U3.1.11
unnamed: J6.6, U3.1.14
unnamed: J6.7, U3.1.12
unnamed: J6.8, U3.1.13
unnamed: J7.1, U4.1.1
unnamed: J7.2, U4.1.8
unnamed: J7.3, U4.1.2
unnamed: J7.4, U4.1.7
unnamed: J7.5, U4.1.3
unnamed: J7.6, U4.1.6
unnamed: J7.7, U4.1.4
unnamed: J7.8, U4.1.5
unnamed: J8.1, U4.1.9
unnamed: J8.2, U4.1.16
unnamed: J8.3, U4.1.10
unnamed: J8.4, U4.1.15
unnamed: J8.5, U4.1.11
unnamed: J8.6, U4.1.14
unnamed: J8.7, U4.1.12
unnamed: J8.8, U4.1.13
unnamed: J9.2, Q1.3 (E)
unnamed: A4.1.6, J11.1
unnamed: A4.1.5, J11.2
unnamed: A4.1.4, J11.3
unnamed: A4.1.3, J11.4
unnamed: A2.2.2, J12.1, J18.2
unnamed: A2.2.3, J13.1, J18.3
unnamed: A2.1.5, J17.5
unnamed: A2.1.8, J17.8
unnamed: A2.2.4, J18.4, Q1.1 (B)
unnamed: A2.2.5, J18.5
unnamed: A2.2.6, J18.6
unnamed: A2.4.6, J19.1
unnamed: A2.4.5, J19.2
unnamed: A2.4.4, J19.3
unnamed: A2.4.3, J19.4
unnamed: A2.4.2, J19.5
unnamed: A2.4.1, J19.6
unnamed: A1.8, J15.8, U1.2.6
SCL: A1.3, J15.3
SDA: A1.2, J15.2

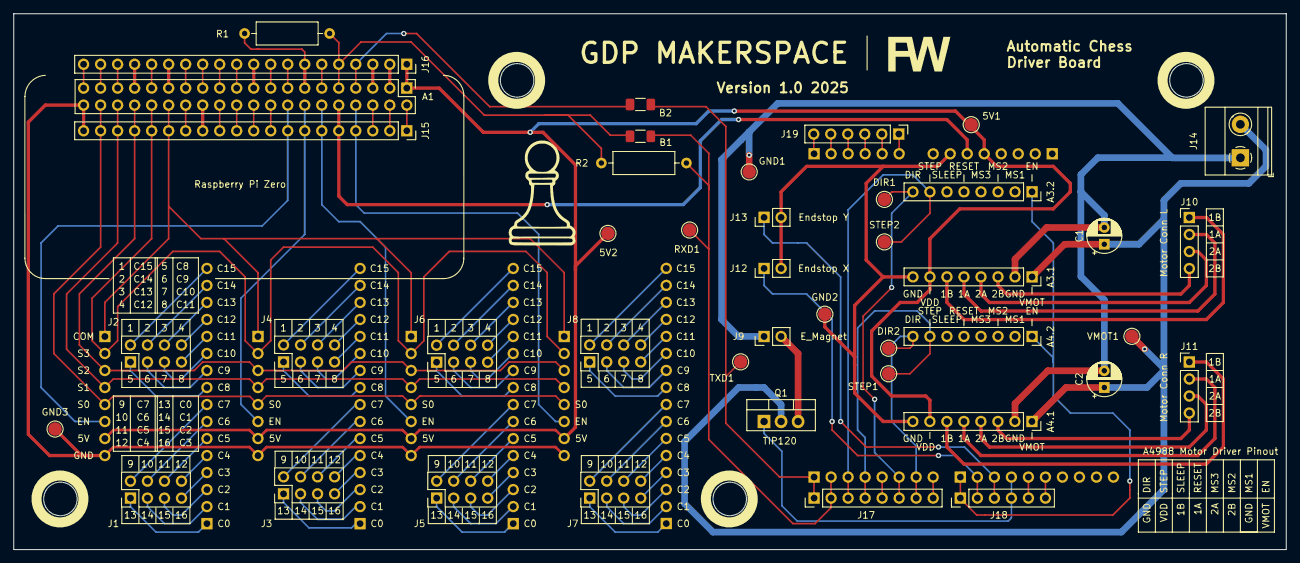
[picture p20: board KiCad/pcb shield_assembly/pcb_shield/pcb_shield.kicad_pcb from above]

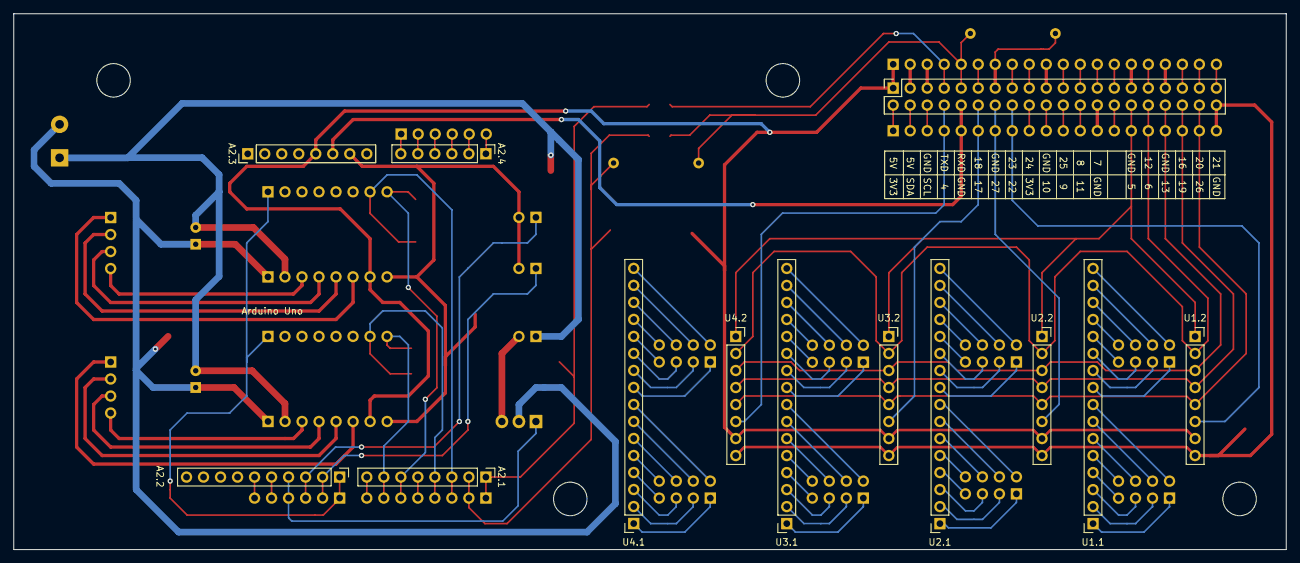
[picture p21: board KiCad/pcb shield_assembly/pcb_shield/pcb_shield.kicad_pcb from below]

Board: 2 copper layers, 190.0 x 80.0 mm, 55 parts (13 on the bottom side), 127 nets.

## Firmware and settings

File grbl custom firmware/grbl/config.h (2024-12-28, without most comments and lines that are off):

#define config_h
#include "grbl.h" // For Arduino IDE compatibility.
#define GDP_CHESS_360MM_360MM
#define CPU_MAP_ATMEGA328P // Arduino Uno CPU
#define BAUD_RATE 115200
#define CMD_RESET 0x18 // ctrl-x.
#define CMD_STATUS_REPORT '?'
#define CMD_CYCLE_START '~'
#define CMD_FEED_HOLD '!'
#define CMD_SAFETY_DOOR 0x84
#define CMD_JOG_CANCEL  0x85
#define CMD_DEBUG_REPORT 0x86 // Only when DEBUG enabled, sends debug report in '{}' braces.
#define CMD_FEED_OVR_RESET 0x90         // Restores feed override value to 100%.
#define CMD_FEED_OVR_COARSE_PLUS 0x91
#define CMD_FEED_OVR_COARSE_MINUS 0x92
#define CMD_FEED_OVR_FINE_PLUS  0x93
#define CMD_FEED_OVR_FINE_MINUS  0x94
#define CMD_RAPID_OVR_RESET 0x95        // Restores rapid override value to 100%.
#define CMD_RAPID_OVR_MEDIUM 0x96
#define CMD_RAPID_OVR_LOW 0x97
#define CMD_SPINDLE_OVR_RESET 0x99      // Restores spindle override value to 100%.
#define CMD_SPINDLE_OVR_COARSE_PLUS 0x9A
#define CMD_SPINDLE_OVR_COARSE_MINUS 0x9B
#define CMD_SPINDLE_OVR_FINE_PLUS 0x9C
#define CMD_SPINDLE_OVR_FINE_MINUS 0x9D
#define CMD_SPINDLE_OVR_STOP 0x9E
#define CMD_COOLANT_FLOOD_OVR_TOGGLE 0xA0
#define CMD_COOLANT_MIST_OVR_TOGGLE 0xA1
#define HOMING_INIT_LOCK // Comment to disable
#define HOMING_CYCLE_0 (1<<Y_AXIS)  // COREXY COMPATIBLE: First home Y
#define HOMING_CYCLE_1 (1<<X_AXIS)  // COREXY COMPATIBLE: Then home X
#define N_HOMING_LOCATE_CYCLE 1 // Integer (1-128)
#define N_STARTUP_LINE 2 // Integer (1-2)
#define N_DECIMAL_COORDVALUE_INCH 4 // Coordinate or position value in inches
#define N_DECIMAL_COORDVALUE_MM   3 // Coordinate or position value in mm
#define N_DECIMAL_RATEVALUE_INCH  1 // Rate or velocity value in in/min
#define N_DECIMAL_RATEVALUE_MM    0 // Rate or velocity value in mm/min
#define N_DECIMAL_SETTINGVALUE    3 // Decimals for floating point setting values
#define N_DECIMAL_RPMVALUE        0 // RPM value in rotations per min.
#define MESSAGE_PROBE_COORDINATES // Enabled by default. Comment to disable.
#define SAFETY_DOOR_SPINDLE_DELAY 4.0 // Float (seconds)
#define SAFETY_DOOR_COOLANT_DELAY 1.0 // Float (seconds)
#define COREXY // Default disabled. Uncomment to enable.
#define CHECK_LIMITS_AT_INIT
#define DEFAULT_FEED_OVERRIDE           100 // 100%. Don't change this value.
#define MAX_FEED_RATE_OVERRIDE          200 // Percent of programmed feed rate (100-255). Usually 120% or 200%
#define MIN_FEED_RATE_OVERRIDE           10 // Percent of programmed feed rate (1-100). Usually 50% or 1%
#define FEED_OVERRIDE_COARSE_INCREMENT   10 // (1-99). Usually 10%.
#define FEED_OVERRIDE_FINE_INCREMENT      1 // (1-99). Usually 1%.
#define DEFAULT_RAPID_OVERRIDE  100 // 100%. Don't change this value.
#define RAPID_OVERRIDE_MEDIUM    50 // Percent of rapid (1-99). Usually 50%.
#define RAPID_OVERRIDE_LOW       25 // Percent of rapid (1-99). Usually 25%.
#define DEFAULT_SPINDLE_SPEED_OVERRIDE    100 // 100%. Don't change this value.
#define MAX_SPINDLE_SPEED_OVERRIDE        200 // Percent of programmed spindle speed (100-255). Usually 200%.
#define MIN_SPINDLE_SPEED_OVERRIDE         10 // Percent of programmed spindle speed (1-100). Usually 10%.
#define SPINDLE_OVERRIDE_COARSE_INCREMENT  10 // (1-99). Usually 10%.
#define SPINDLE_OVERRIDE_FINE_INCREMENT     1 // (1-99). Usually 1%.
#define RESTORE_OVERRIDES_AFTER_PROGRAM_END // Default enabled. Comment to disable.
#define REPORT_FIELD_BUFFER_STATE // Default enabled. Comment to disable.
#define REPORT_FIELD_PIN_STATE // Default enabled. Comment to disable.
#define REPORT_FIELD_CURRENT_FEED_SPEED // Default enabled. Comment to disable.
#define REPORT_FIELD_WORK_COORD_OFFSET // Default enabled. Comment to disable.
#define REPORT_FIELD_OVERRIDES // Default enabled. Comment to disable.
#define REPORT_FIELD_LINE_NUMBERS // Default enabled. Comment to disable.
#define REPORT_OVR_REFRESH_BUSY_COUNT 20  // (1-255)
#define REPORT_OVR_REFRESH_IDLE_COUNT 10  // (1-255) Must be less than or equal to the busy count
#define REPORT_WCO_REFRESH_BUSY_COUNT 30  // (2-255)
#define REPORT_WCO_REFRESH_IDLE_COUNT 10  // (2-255) Must be less than or equal to the busy count
#define ACCELERATION_TICKS_PER_SECOND 100
#define ADAPTIVE_MULTI_AXIS_STEP_SMOOTHING  // Default enabled. Comment to disable.
#define TOOL_LENGTH_OFFSET_AXIS Z_AXIS // Default z-axis. Valid values are X_AXIS, Y_AXIS, or Z_AXIS.
#define VARIABLE_SPINDLE // Default enabled. Comment to disable.
#define MINIMUM_JUNCTION_SPEED 0.0 // (mm/min)
#define MINIMUM_FEED_RATE 1.0 // (mm/min)
#define N_ARC_CORRECTION 12 // Integer (1-255)
#define ARC_ANGULAR_TRAVEL_EPSILON 5E-7 // Float (radians)
#define DWELL_TIME_STEP 50 // Integer (1-255) (milliseconds)
#define ENABLE_RESTORE_EEPROM_WIPE_ALL         // '$RST=*' Default enabled. Comment to disable.
#define ENABLE_RESTORE_EEPROM_DEFAULT_SETTINGS // '$RST=$' Default enabled. Comment to disable.
#define ENABLE_RESTORE_EEPROM_CLEAR_PARAMETERS // '$RST=#' Default enabled. Comment to disable.
#define ENABLE_BUILD_INFO_WRITE_COMMAND // '$I=' Default enabled. Comment to disable.
#define FORCE_BUFFER_SYNC_DURING_EEPROM_WRITE // Default enabled. Comment to disable.
#define FORCE_BUFFER_SYNC_DURING_WCO_CHANGE // Default enabled. Comment to disable.
#define PARKING_AXIS Z_AXIS // Define which axis that performs the parking motion
#define PARKING_TARGET -5.0 // Parking axis target. In mm, as machine coordinate [-max_travel,0].
#define PARKING_RATE 500.0 // Parking fast rate after pull-out in mm/min.
#define PARKING_PULLOUT_RATE 100.0 // Pull-out/plunge slow feed rate in mm/min.
#define PARKING_PULLOUT_INCREMENT 5.0 // Spindle pull-out and plunge distance in mm. Incremental distance.
#define DISABLE_LASER_DURING_HOLD // Default enabled. Comment to disable.
#define N_PIECES 4  // Integer (1-4). Number of piecewise lines used in script solution.
#define RPM_MAX  11686.4  // Max RPM of model. $30 > RPM_MAX will be limited to RPM_MAX.
#define RPM_MIN  202.5    // Min RPM of model. $31 < RPM_MIN will be limited to RPM_MIN.
#define RPM_POINT12  6145.4  // Used N_PIECES >=2. Junction point between lines 1 and 2.
#define RPM_POINT23  9627.8  // Used N_PIECES >=3. Junction point between lines 2 and 3.
#define RPM_POINT34  10813.9 // Used N_PIECES = 4. Junction point between lines 3 and 4.
#define RPM_LINE_A1  3.197101e-03  // Used N_PIECES >=1. A and B constants of line 1.
#define RPM_LINE_B1  -3.526076e-1
#define RPM_LINE_A2  1.722950e-2   // Used N_PIECES >=2. A and B constants of line 2.
#define RPM_LINE_B2  8.588176e+01
#define RPM_LINE_A3  5.901518e-02  // Used N_PIECES >=3. A and B constants of line 3.
#define RPM_LINE_B3  4.881851e+02
#define RPM_LINE_A4  1.203413e-01  // Used N_PIECES = 4. A and B constants of line 4.
#define RPM_LINE_B4  1.151360e+03
#define DUAL_AXIS_SELECT  X_AXIS  // Must be either X_AXIS or Y_AXIS
#define DUAL_AXIS_HOMING_FAIL_AXIS_LENGTH_PERCENT  5.0  // Float (percent)
#define DUAL_AXIS_HOMING_FAIL_DISTANCE_MAX  25.0  // Float (mm)
#define DUAL_AXIS_HOMING_FAIL_DISTANCE_MIN  2.5  // Float (mm)
#define DUAL_AXIS_CONFIG_PROTONEER_V3_51    // Uncomment to select. Comment other configs.

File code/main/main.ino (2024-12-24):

/*
main.ino

This is the main script for the motor movement in a CoreXY system. 

(c)2024 Felix Wittwer
*/

String serialtext; // for incoming serial data
int stepCounter;
int steps = 0;

//variables for motorsystem
int speedm = 750;
int mtogo = 0; //motor one steps to go
int ntogo = 0; //motor two steps to go

//variables for xy coordinate system
int curx = 0; //current x
int cury = 0; //current y
int xtogo = 0;
int ytogo = 0;

//IO variables
int m1enpin = 3;
int m1steppin = 5;
int m1dirpin = 4;
int m2enpin = 10;
int m2steppin = 9;
int m2dirpin = 8;
//endstops
int xstop = 12;
int ystop = 13;
//magnet
int magnetpin = 2;
bool magnetstatus = false;

void setup(){
  pinMode(m1enpin, OUTPUT);
  pinMode(m1steppin, OUTPUT);
  pinMode(m1dirpin, OUTPUT);
  pinMode(m2enpin, OUTPUT);
  pinMode(m2steppin, OUTPUT);
  pinMode(m2dirpin, OUTPUT);
  pinMode(magnetpin, OUTPUT);
  pinMode(xstop, INPUT);
  pinMode(ystop, INPUT);
  Serial.begin(115200); //Make shure the baudrate is high enough for your pupouse. When too low it could hinder the execution of the code. This is in the case of motorcontrol with very small delays crucial. 
  digitalWrite(m1enpin, HIGH);
  digitalWrite(m2enpin, HIGH);
}

void loop(){
  if (Serial.available() > 0) {
    serialtext = Serial.readString();
    //change process variables based on given arguments by the serial connection
    if (serialtext.startsWith("X")){
      serialtext.remove(0,1);
      Serial.print(serialtext);
      xtogo += serialtext.toInt();
    }
    if (serialtext.startsWith("Y")){
      serialtext.remove(0,1);
      Serial.print(serialtext);
      ytogo += serialtext.toInt();
    }
    if (serialtext.startsWith("M")){
      serialtext.remove(0,1);
      Serial.println("Magnet");
      if (magnetstatus == false){
        magnetstatus = true;
        digitalWrite(magnetpin, HIGH);
      } else if (magnetstatus == true){
        magnetstatus = false;
        digitalWrite(magnetpin, LOW);
      }
    }
    if (serialtext.startsWith("S")){
      serialtext.remove(0,1);
      Serial.print("Speed set to: ");
      Serial.print(serialtext);
      speedm = serialtext.toInt();
    }
    if (serialtext.startsWith("G")){
      movement();
    }
  }
}

void movement(){
  //calculate steps for each motor
  mtogo = xtogo + ytogo;
  ntogo = xtogo - ytogo;
  while (mtogo != 0 or ntogo != 0) {
    // if (mtogo = 0){
    //   motor(speedm, m2enpin, ntogo, m2steppin, m2dirpin);
    //   ntogo = 0;
    // }
    // if (ntogo = 0){
    //   motor(speedm, m1enpin, mtogo, m1steppin, m1dirpin);
    //   mtogo = 0;
    // }
    if (mtogo != 0){
      if (mtogo < 0){
        motor(speedm, m1enpin, -1, m1steppin, m1dirpin);
        mtogo = mtogo + 1;
      }
      if (mtogo > 0){
        motor(speedm, m1enpin, 1, m1steppin, m1dirpin);
        mtogo = mtogo - 1;
      }
    }
    if (ntogo != 0){
      if (ntogo < 0){
        motor(speedm, m2enpin, -1, m2steppin, m2dirpin);
        ntogo = ntogo + 1;
      }
      if (ntogo > 0){
        motor(speedm, m2enpin, 1, m2steppin, m2dirpin);
        ntogo = ntogo - 1;
      }
    }
    Serial.print(mtogo);
    Serial.print(",");
    Serial.println(ntogo);
  }
  Serial.println("finished");
  // digitalWrite(m1enpin, HIGH);
  // digitalWrite(m2enpin, HIGH);
  xtogo = 0;
  ytogo = 0;
}

void motor(int speedm,int enpin, int steps, int steppin, int dirpin){
  digitalWrite(enpin, LOW);
  if (steps > 0){
    digitalWrite(dirpin, LOW);
  }else if (steps < 0){
    digitalWrite(dirpin, HIGH);
  }
  steps = abs(steps);
  for(stepCounter = 0; stepCounter <= steps; stepCounter++) {
    digitalWrite(steppin,HIGH);
    delayMicroseconds(speedm);
    digitalWrite(steppin,LOW);
    delayMicroseconds(speedm);
//      Serial.println(stepCounter);
  }
  digitalWrite(enpin, HIGH);
}

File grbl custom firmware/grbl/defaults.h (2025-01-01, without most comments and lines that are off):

#ifdef DEFAULTS_GENERIC
  #define DEFAULT_X_STEPS_PER_MM 250.0
  #define DEFAULT_Y_STEPS_PER_MM 250.0
  #define DEFAULT_Z_STEPS_PER_MM 250.0
  #define DEFAULT_X_MAX_RATE 500.0 // mm/min
  #define DEFAULT_Y_MAX_RATE 500.0 // mm/min
  #define DEFAULT_Z_MAX_RATE 500.0 // mm/min
  #define DEFAULT_X_ACCELERATION (10.0*60*60) // 10*60*60 mm/min^2 = 10 mm/sec^2
  #define DEFAULT_Y_ACCELERATION (10.0*60*60) // 10*60*60 mm/min^2 = 10 mm/sec^2
  #define DEFAULT_Z_ACCELERATION (10.0*60*60) // 10*60*60 mm/min^2 = 10 mm/sec^2
  #define DEFAULT_X_MAX_TRAVEL 200.0 // mm NOTE: Must be a positive value.
  #define DEFAULT_Y_MAX_TRAVEL 200.0 // mm NOTE: Must be a positive value.
  #define DEFAULT_Z_MAX_TRAVEL 200.0 // mm NOTE: Must be a positive value.
  #define DEFAULT_SPINDLE_RPM_MAX 1000.0 // rpm
  #define DEFAULT_SPINDLE_RPM_MIN 0.0 // rpm
  #define DEFAULT_STEP_PULSE_MICROSECONDS 10
  #define DEFAULT_STEPPING_INVERT_MASK 0
  #define DEFAULT_DIRECTION_INVERT_MASK 0
  #define DEFAULT_STEPPER_IDLE_LOCK_TIME 25 // msec (0-254, 255 keeps steppers enabled)
  #define DEFAULT_STATUS_REPORT_MASK 1 // MPos enabled
  #define DEFAULT_JUNCTION_DEVIATION 0.01 // mm
  #define DEFAULT_ARC_TOLERANCE 0.002 // mm
  #define DEFAULT_REPORT_INCHES 0 // false
  #define DEFAULT_INVERT_ST_ENABLE 0 // false
  #define DEFAULT_INVERT_LIMIT_PINS 0 // false
  #define DEFAULT_SOFT_LIMIT_ENABLE 0 // false
  #define DEFAULT_HARD_LIMIT_ENABLE 0  // false
  #define DEFAULT_INVERT_PROBE_PIN 0 // false
  #define DEFAULT_LASER_MODE 0 // false
  #define DEFAULT_HOMING_ENABLE 0  // false
  #define DEFAULT_HOMING_DIR_MASK 0 // move positive dir
  #define DEFAULT_HOMING_FEED_RATE 25.0 // mm/min
  #define DEFAULT_HOMING_SEEK_RATE 500.0 // mm/min
  #define DEFAULT_HOMING_DEBOUNCE_DELAY 250 // msec (0-65k)
  #define DEFAULT_HOMING_PULLOFF 1.0 // mm
#endif
  #define DEFAULT_X_STEPS_PER_MM 5.0
  #define DEFAULT_Y_STEPS_PER_MM 5.0
  #define DEFAULT_Z_STEPS_PER_MM 5.0
  #define DEFAULT_X_MAX_RATE 10000.0 // mm/min
  #define DEFAULT_Y_MAX_RATE 10000.0 // mm/min
  #define DEFAULT_Z_MAX_RATE 10000.0 // mm/min
  #define DEFAULT_X_ACCELERATION 5000 // mm/min^2
  #define DEFAULT_Y_ACCELERATION 5000 // mm/min^2
  #define DEFAULT_Z_ACCELERATION 5000 // mm/min^2
  #define DEFAULT_X_MAX_TRAVEL 350.0 // mm NOTE: Must be a positive value.
  #define DEFAULT_Y_MAX_TRAVEL 390.0 // mm NOTE: Must be a positive value.
  #define DEFAULT_Z_MAX_TRAVEL 360.0 // mm NOTE: Must be a positive value.
  #define DEFAULT_SPINDLE_RPM_MAX 1000.0 // rpm
  #define DEFAULT_SPINDLE_RPM_MIN 0.0 // rpm
  #define DEFAULT_STEP_PULSE_MICROSECONDS 10
  #define DEFAULT_STEPPING_INVERT_MASK 0
  #define DEFAULT_DIRECTION_INVERT_MASK 0
  #define DEFAULT_STEPPER_IDLE_LOCK_TIME 25 // msec (0-254, 255 keeps steppers enabled)
  #define DEFAULT_STATUS_REPORT_MASK 1 // MPos enabled
  #define DEFAULT_JUNCTION_DEVIATION 0.01 // mm
  #define DEFAULT_ARC_TOLERANCE 0.002 // mm
  #define DEFAULT_REPORT_INCHES 0 // false
  #define DEFAULT_INVERT_ST_ENABLE 0 // false
  #define DEFAULT_INVERT_LIMIT_PINS 0 // false
  #define DEFAULT_SOFT_LIMIT_ENABLE 0 // false
  #define DEFAULT_HARD_LIMIT_ENABLE 0  // false
  #define DEFAULT_INVERT_PROBE_PIN 0 // false
  #define DEFAULT_LASER_MODE 1 // true
  #define DEFAULT_HOMING_ENABLE 1  // true
  #define DEFAULT_HOMING_DIR_MASK 0 // move positive dir
  #define DEFAULT_HOMING_FEED_RATE 25.0 // mm/min
  #define DEFAULT_HOMING_SEEK_RATE 7000.0 // mm/min
  #define DEFAULT_HOMING_DEBOUNCE_DELAY 250 // msec (0-65k)
  #define DEFAULT_HOMING_PULLOFF 1.0 // mm
#ifdef DEFAULTS_SHERLINE_5400
  #define MICROSTEPS 2
  #define STEPS_PER_REV 200.0
  #define MM_PER_REV (0.050*MM_PER_INCH) // 0.050 inch/rev leadscrew
  #define DEFAULT_X_STEPS_PER_MM (STEPS_PER_REV*MICROSTEPS/MM_PER_REV)
  #define DEFAULT_Y_STEPS_PER_MM (STEPS_PER_REV*MICROSTEPS/MM_PER_REV)
  #define DEFAULT_Z_STEPS_PER_MM (STEPS_PER_REV*MICROSTEPS/MM_PER_REV)
  #define DEFAULT_X_MAX_RATE 635.0 // mm/min (25 ipm)
  #define DEFAULT_Y_MAX_RATE 635.0 // mm/min
  #define DEFAULT_Z_MAX_RATE 635.0 // mm/min
  #define DEFAULT_X_ACCELERATION (50.0*60*60) // 50*60*60 mm/min^2 = 50 mm/sec^2
  #define DEFAULT_Y_ACCELERATION (50.0*60*60) // 50*60*60 mm/min^2 = 50 mm/sec^2
  #define DEFAULT_Z_ACCELERATION (50.0*60*60) // 50*60*60 mm/min^2 = 50 mm/sec^2
  #define DEFAULT_X_MAX_TRAVEL 225.0 // mm NOTE: Must be a positive value.
  #define DEFAULT_Y_MAX_TRAVEL 125.0 // mm NOTE: Must be a positive value.
  #define DEFAULT_Z_MAX_TRAVEL 170.0 // mm NOTE: Must be a positive value.
  #define DEFAULT_SPINDLE_RPM_MAX 2800.0 // rpm
  #define DEFAULT_SPINDLE_RPM_MIN 0.0 // rpm
  #define DEFAULT_STEP_PULSE_MICROSECONDS 10
  #define DEFAULT_STEPPING_INVERT_MASK 0
  #define DEFAULT_DIRECTION_INVERT_MASK ((1<<Y_AXIS)|(1<<Z_AXIS))
  #define DEFAULT_STEPPER_IDLE_LOCK_TIME 25 // msec (0-254, 255 keeps steppers enabled)
  #define DEFAULT_STATUS_REPORT_MASK 1 // MPos enabled
  #define DEFAULT_JUNCTION_DEVIATION 0.01 // mm
  #define DEFAULT_ARC_TOLERANCE 0.002 // mm
  #define DEFAULT_REPORT_INCHES 0 // true
  #define DEFAULT_INVERT_ST_ENABLE 0 // false
  #define DEFAULT_INVERT_LIMIT_PINS 0 // false
  #define DEFAULT_SOFT_LIMIT_ENABLE 0 // false
  #define DEFAULT_HARD_LIMIT_ENABLE 0  // false
  #define DEFAULT_INVERT_PROBE_PIN 0 // false
  #define DEFAULT_LASER_MODE 0 // false
  #define DEFAULT_HOMING_ENABLE 0  // false
  #define DEFAULT_HOMING_DIR_MASK 0 // move positive dir
  #define DEFAULT_HOMING_FEED_RATE 50.0 // mm/min
  #define DEFAULT_HOMING_SEEK_RATE 635.0 // mm/min
  #define DEFAULT_HOMING_DEBOUNCE_DELAY 250 // msec (0-65k)
  #define DEFAULT_HOMING_PULLOFF 1.0 // mm
#endif
#ifdef DEFAULTS_POCKETNC_FR4
  #define DEFAULT_X_STEPS_PER_MM 800.0
  #define DEFAULT_Y_STEPS_PER_MM 800.0
  #define DEFAULT_Z_STEPS_PER_MM 800.0
  #define DEFAULT_X_MAX_RATE 300.0 // mm/min
  #define DEFAULT_Y_MAX_RATE 300.0 // mm/min
  #define DEFAULT_Z_MAX_RATE 300.0 // mm/min
  #define DEFAULT_X_ACCELERATION (30.0*60*60) // 15*60*60 mm/min^2 = 15 mm/sec^2
  #define DEFAULT_Y_ACCELERATION (30.0*60*60) // 15*60*60 mm/min^2 = 15 mm/sec^2
  #define DEFAULT_Z_ACCELERATION (30.0*60*60) // 15*60*60 mm/min^2 = 15 mm/sec^2
  #define DEFAULT_X_MAX_TRAVEL 225.0 // mm NOTE: Must be a positive value.
  #define DEFAULT_Y_MAX_TRAVEL 125.0 // mm NOTE: Must be a positive value.
  #define DEFAULT_Z_MAX_TRAVEL 170.0 // mm NOTE: Must be a positive value.
  #define DEFAULT_SPINDLE_RPM_MAX 7000.0 // rpm
  #define DEFAULT_SPINDLE_RPM_MIN 0.0 // rpm
  #define DEFAULT_STEP_PULSE_MICROSECONDS 10
  #define DEFAULT_STEPPING_INVERT_MASK 0
  #define DEFAULT_DIRECTION_INVERT_MASK ((1<<Y_AXIS)|(1<<Z_AXIS))
  #define DEFAULT_STEPPER_IDLE_LOCK_TIME 250 // msec (0-254, 255 keeps steppers enabled)
  #define DEFAULT_STATUS_REPORT_MASK 3 // WPos enabled
  #define DEFAULT_JUNCTION_DEVIATION 0.01 // mm
  #define DEFAULT_ARC_TOLERANCE 0.002 // mm
  #define DEFAULT_REPORT_INCHES 0 // false
  #define DEFAULT_INVERT_ST_ENABLE 1 // false
  #define DEFAULT_INVERT_LIMIT_PINS 0 // false
  #define DEFAULT_SOFT_LIMIT_ENABLE 0 // false
  #define DEFAULT_HARD_LIMIT_ENABLE 0  // false
  #define DEFAULT_INVERT_PROBE_PIN 0 // false
  #define DEFAULT_LASER_MODE 0 // false
  #define DEFAULT_HOMING_ENABLE 1  // false
  #define DEFAULT_HOMING_DIR_MASK 1 // move positive dir
  #define DEFAULT_HOMING_FEED_RATE 100.0 // mm/min
  #define DEFAULT_HOMING_SEEK_RATE 300.0 // mm/min
  #define DEFAULT_HOMING_DEBOUNCE_DELAY 250 // msec (0-65k)
  #define DEFAULT_HOMING_PULLOFF 3.0 // mm
#endif
#ifdef DEFAULTS_SHAPEOKO
  #define MICROSTEPS_XY 8
  #define STEP_REVS_XY 400
  #define MM_PER_REV_XY (0.08*18*MM_PER_INCH) // 0.08 in belt pitch, 18 pulley teeth
  #define MICROSTEPS_Z 2
  #define STEP_REVS_Z 400
  #define MM_PER_REV_Z 1.250 // 1.25 mm/rev leadscrew
  #define DEFAULT_X_STEPS_PER_MM (MICROSTEPS_XY*STEP_REVS_XY/MM_PER_REV_XY)
  #define DEFAULT_Y_STEPS_PER_MM (MICROSTEPS_XY*STEP_REVS_XY/MM_PER_REV_XY)
  #define DEFAULT_Z_STEPS_PER_MM (MICROSTEPS_Z*STEP_REVS_Z/MM_PER_REV_Z)
  #define DEFAULT_X_MAX_RATE 1000.0 // mm/min
  #define DEFAULT_Y_MAX_RATE 1000.0 // mm/min
  #define DEFAULT_Z_MAX_RATE 1000.0 // mm/min
  #define DEFAULT_X_ACCELERATION (15.0*60*60) // 15*60*60 mm/min^2 = 15 mm/sec^2
  #define DEFAULT_Y_ACCELERATION (15.0*60*60) // 15*60*60 mm/min^2 = 15 mm/sec^2
  #define DEFAULT_Z_ACCELERATION (15.0*60*60) // 15*60*60 mm/min^2 = 15 mm/sec^2
  #define DEFAULT_X_MAX_TRAVEL 200.0 // mm NOTE: Must be a positive value.
  #define DEFAULT_Y_MAX_TRAVEL 200.0 // mm NOTE: Must be a positive value.
  #define DEFAULT_Z_MAX_TRAVEL 200.0 // mm NOTE: Must be a positive value.
  #define DEFAULT_SPINDLE_RPM_MAX 10000.0 // rpm
  #define DEFAULT_SPINDLE_RPM_MIN 0.0 // rpm
  #define DEFAULT_STEP_PULSE_MICROSECONDS 10
  #define DEFAULT_STEPPING_INVERT_MASK 0
  #define DEFAULT_DIRECTION_INVERT_MASK ((1<<Y_AXIS)|(1<<Z_AXIS))
  #define DEFAULT_STEPPER_IDLE_LOCK_TIME 255 // msec (0-254, 255 keeps steppers enabled)
  #define DEFAULT_STATUS_REPORT_MASK 1 // MPos enabled
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

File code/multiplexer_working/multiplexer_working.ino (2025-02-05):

//Mux control pins
int en = 7;
int s0 = 8;
int s1 = 9;
int s2 = 10;
int s3 = 11;


//Mux in "SIG" pin
int SIG_pin = 3;

void setup() {
  pinMode(en, OUTPUT);
  pinMode(s0, OUTPUT);
  pinMode(s1, OUTPUT);
  pinMode(s2, OUTPUT);
  pinMode(s3, OUTPUT);
  
  pinMode(SIG_pin, INPUT);

  digitalWrite(en, LOW);
  digitalWrite(s0, LOW);
  digitalWrite(s1, LOW);
  digitalWrite(s2, LOW);
  digitalWrite(s3, LOW);

  Serial.begin(9600);
}

void loop() {

  //Loop through and read all 16 values
  for (int i = 0; i < 16; i ++) {
    Serial.print("Value at channel ");
    Serial.print(i); Serial.print("is : ");
    Serial.println(readMux(i));
    delay(300);
  }
}

int readMux(int channel) {
  int controlPin[] = {s0, s1, s2, s3};
  int muxChannel[16][4] = { {0, 0, 0, 0},
                            {1, 0, 0, 0},
                            {0, 1, 0, 0},
                            {1, 1, 0, 0},
                            {0, 0, 1, 0},
                            {1, 0, 1, 0},
                            {0, 1, 1, 0},
                            {1, 1, 1, 0},
                            {0, 0, 0, 1},
                            {1, 0, 0, 1},
                            {0, 1, 0, 1},
                            {1, 1, 0, 1},
                            {0, 0, 1, 1},
                            {1, 0, 1, 1},
                            {0, 1, 1, 1},
                            {1, 1, 1, 1}
                          };
  //loop through the 4 sig
  for (int i = 0; i < 4; i ++) {
    digitalWrite(controlPin[i], muxChannel[channel][i]);
  }
  //read the value at the SIG pin
  int val = digitalRead(SIG_pin); //return the value
  return val;
}

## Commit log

2024-09-18 create file for testing a single stepper motor
2024-09-24 add dual motor control
    with static values and direction
2024-10-01 build terminal like control of motors via serial monitor
2024-10-02 add superposition motor control
2024-10-16 add KiCad files
    [circuit_and_pcb.kicad_pcb, circuit_and_pcb.kicad_sch]
2024-10-16 finish motor diagram
    [circuit_and_pcb.kicad_sch]
2024-10-16 add circuit diagrams to README
2024-11-26 add script for controlling the motors individually
2024-12-01 add motortester script
    Add script to test and understand functionality of a singe motor by manually inputing the parameters over serial.
2024-12-21 add customized 3d files
    [Pulley_Support_B.stl, Pulley_Support_B_new.stl]
2024-12-22 modifying support pully A and B files add stl and sliced files for 3D printing
    [Pulley_Support_A.stl, Pulley_Support_A_new.stl]
2024-12-24 add magnet functionality
2024-12-25 add custom grbl firmware files
    [config.h, cpu_map.h, defaults.h]
2024-12-25 update README with grbl installation info
2024-12-28 add settings preset for our coreXY machine
    [config.h, defaults.h]
2025-01-01 enable and setup homing and add starting routine with G-Code
    [defaults.h]
2025-01-01 add magnet commands
2025-01-05 reorder files and further try to interface grbl wiht python
2025-01-05 extend circuit diagram
    [Pulley_Support_A.stl, Pulley_Support_A_new.stl, Pulley_Support_B.stl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]
2025-02-05 add multiplexer code
    [circuit_and_pcb.kicad_sch]
2025-04-08 KiCad stuff for PCB
    [pcb_shield.kicad_pcb, pcb_shield.kicad_sch]
2025-04-08 add main parts
    [pcb_shield.kicad_sch]
2025-04-08 start with pcb
    [pcb_shield.kicad_pcb, pcb_shield.kicad_sch]
2025-04-08 adding multiplexers
    [pcb_shield.kicad_pcb, pcb_shield.kicad_sch]
2025-04-08 almost finished pcb
    [pcb_shield.kicad_pcb, pcb_shield.kicad_sch]
2025-04-09 add aditional headers
    [pcb_shield.kicad_pcb, pcb_shield.kicad_sch]
2025-04-12 working on PCB and creating manufacturing files
    [pcb_shield-B_Cu.gbr, pcb_shield-B_Mask.gbr, pcb_shield-B_Paste.gbr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]
2025-04-13 add files for pcb assembly
    [BOMxlsx.xlsx, Sample-BOM_JLCSMT.xlsx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]
2025-04-13 make files for hackclub pcb grant
    [pcb_shield-B_Cu.gbr, pcb_shield-B_Mask.gbr, pcb_shield-B_Paste.gbr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]
2025-05-27 adding 3d files for organisation parts
    [Cable_clips_for_zipties.stl, PCB_holder.stl, small cable clip.stl]
2025-05-29 adding mount pieces for plexiglas sheet
    [A_Plexiglasmount.stl, B_Plexiglasmount.stl, Motor_A_Plexiglasmount.stl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]

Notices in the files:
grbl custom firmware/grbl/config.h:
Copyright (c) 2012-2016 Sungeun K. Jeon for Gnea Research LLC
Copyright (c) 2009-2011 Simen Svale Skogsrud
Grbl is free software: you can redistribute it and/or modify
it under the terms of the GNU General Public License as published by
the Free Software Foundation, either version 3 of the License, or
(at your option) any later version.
